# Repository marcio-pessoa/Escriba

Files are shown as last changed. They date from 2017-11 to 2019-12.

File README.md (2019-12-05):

# Escriba Mark I - Light CNC

## Introduction

Escriba Mark I is a Light CNC machine, capable to use tools like Pens, Laser other kind of stuff.

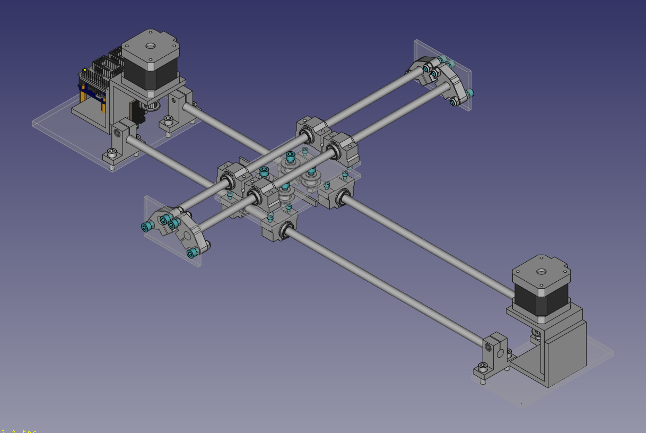
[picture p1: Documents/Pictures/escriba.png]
Escriba


<!---
The bidimentional work area:
- Width: ??? mm
- Height: ??? mm
--->

## Cloning
```
git clone --recurse-submodules https://github.com/marcio-pessoa/Escriba.git
```

## Videos
Watch this projects videos on [YouTube Playlist].

## Changes
All notable changes to this project will be documented in this [Change log](CHANGELOG.md).

## Mechanics
This project uses an original mech made from scratch with the following goals:
- Reliable
- Precise
- Robust
- Well done
- Cheap, but beautiful

Check out [Mechanics](Mechanics/README.md) design to know more.

## Electronics
Arduino and CNC Shield are used to [Electronics](Electronics/README.md) control system.

## Firmware
Grbl is my [Firmware](Firmware/README.md)! :-)

## Tools
Nice [Tools](Tools/README.md) can be used with!

## BOM - Bill of materials
If you want to build your own, take a look at [Bill of materials](BOM.md).

---
[YouTube Playlist]: https://www.youtube.com/watch?v=fAPBSzcztSE&list=PLs1JZHyVhlZUeYavBQfkzo5e3CdledMW0

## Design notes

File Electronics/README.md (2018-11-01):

# Escriba Mark I - Light CNC

[Main page]

## Electronics

### Power supply
Technical specifications:
- Voltage: 12 VDC
- Amperage: 5 A
- Interface: P8 (+ out, - in)

### Arduino
Technical specifications:
- Model: [Arduino Uno] R3

#### Diagram
                                 .-----.
    .----[PWR]-------------------| USB |--.
    |                            '-----'  |
    |         GND/RST2  [ ][ ]            |
    |       MOSI2/SCK2  [ ][ ]  A5/SCL[ ] |   C5
    |          5V/MISO2 [ ][ ]  A4/SDA[ ] |   C4
    |                             AREF[ ] |
    |                              GND[ ] |
    | [ ]NC                     SCK/13[ ] |   B5
    | [ ]v.ref                 MISO/12[ ] |   .
    | [ ]RST                   MOSI/11[ ]~|   .
    | [ ]3V3    +---+               10[ ]~|   .
    | [ ]5v     | A |                9[ ]~|   .
    | [ ]GND   -| R |-               8[ ] |   B0
    | [ ]GND   -| D |-                    |
    | [ ]Vin   -| U |-               7[ ] |   D7
    |          -| I |-               6[ ]~|   .
    | [ ]A0    -| N |-               5[ ]~|   .
    | [ ]A1    -| O |-               4[ ] |   .
    | [ ]A2     +---+           INT1/3[ ]~|   .
    | [ ]A3                     INT0/2[ ] |   .
    | [ ]A4/SDA  RST SCK MISO     TX>1[ ] |   .
    | [ ]A5/SCL  [ ] [ ] [ ]      RX<0[ ] |   D0
    |            [ ] [ ] [ ]              |
    '--.                         .--------'
        \_______________________/

Diagram by http://busyducks.com/ascii-art-arduinos

#### Pin designation
 id | pin |   type    | direction |               description
----|-----|-----------|-----------|--------------------------------------------
  0 |   0 | digital   | input     | Serial communication
  1 |   1 | digital   | output    | Serial communication
  2 |   0 | digital   | output    | Step Pulse x-axis
  3 |   3 | digital   | output    | Step Pulse y-axis
  4 |   4 | digital   | output    | Step Pulse z-axis
  5 |   5 | digital   | output    | Direction x-axis
  6 |   6 | digital   | output    | Direction y-axis
  7 |   7 | digital   | output    | Direction z-axis
  8 |   8 | digital   | output    | Stepper Enable/Disable
  9 |   9 | digital   | input     | Limit x-axis
 10 |  10 | digital   | input     | Limit y-axis
 11 |  11 | PWM       | input     | Limit z-axis
 12 |  12 | digital   | output    | Spindle Enable
 13 |  13 | digital   | output    | Spindle Direction
 14 |   0 | digital   | input     | Reset/Abort
 15 |   1 | digital   | input     | Feed Hold
 16 |   2 | digital   | input     | Cycle Start/Resume
 17 |   3 | digital   | output    | Coolant Enable
 18 |   4 | digital   | input     | (not used/reserved)
 19 |   5 | digital   | input     | Probe

### CNC Shield
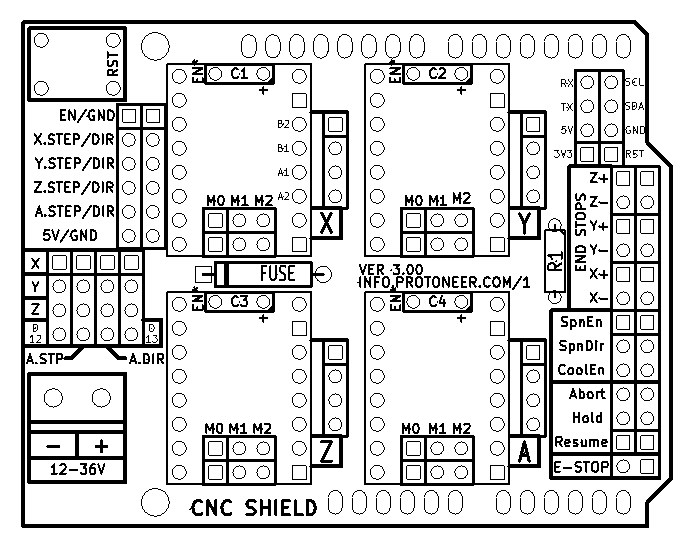
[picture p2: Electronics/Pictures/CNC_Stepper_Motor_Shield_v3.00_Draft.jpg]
PCB description


[CNC/Stepper Motor Shield](../Documents/cnc-3axis-shield.pdf)

Technical specifications:
- Version: 3.00

Connected at:
- Arduino: Digital Pin 11
- CNC Shield: Z+ end stop pin

### Stepper drivers
CNC Shield has 3 jumpers to configure each axes resolution.
That can be set to configure the motor micro stepping.

#### Resolution configuration

##### Pololu A4988
 M0   | M1   | M2   | Microstep resolution
------|------|------|-----------------------
 Low  | Low  | Low  | Full step
 High | Low  | Low  | Half step
 Low  | High | Low  | Quarter step
 High | High | Low  | Eighth step
 High | High | High | Sixteenth step

##### Pololu DRV8825
 M0   | M1   | M2   | Microstep resolution
------|------|------|-----------------------
 Low  | Low  | Low  | Full step
 High | Low  | Low  | Half step
 Low  | High | Low  | 1/4 step
 High | High | Low  | 1/8 step
 Low  | Low  | High | 1/16 step
 High | Low  | High | 1/32 step
 Low  | High | High | 1/32 step
 High | High | High | 1/32 step

### Step motors
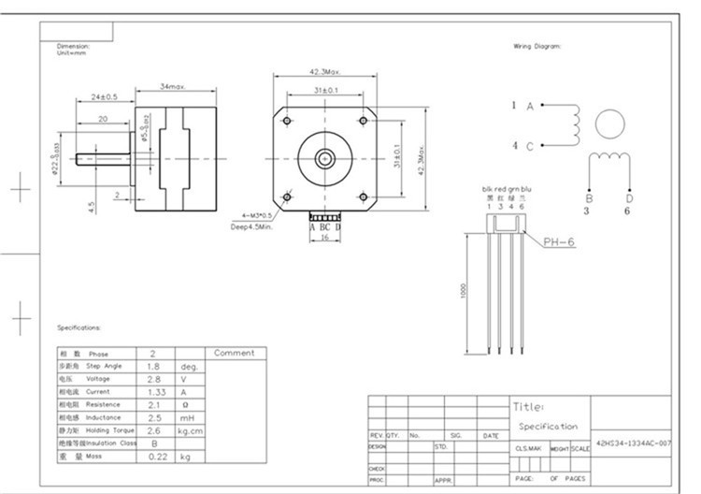
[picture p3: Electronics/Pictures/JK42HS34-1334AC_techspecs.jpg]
Step motors


Technical specifications:
- Model: JK42HS34-1334AC
- Phase: 2
- Step angle: 1.8 degrees (200 steps/revolution)
- Rated voltage: 2.8 V
- Current/Phase: 1.33 A
- Resistance/Phase: 2.1 Ω
- Inductance/Phase: 2.5 mH
- Holding Torque: 22 N·cm (2.6 kg·cm)
- Outlet: 4 wires
- Shaft: 5 mm single flat
- Size (metric): 4.2 cm x 4.2 cm x 3.4 cm
- Size (imperial): 1.65" x 1.65" x 1.34"

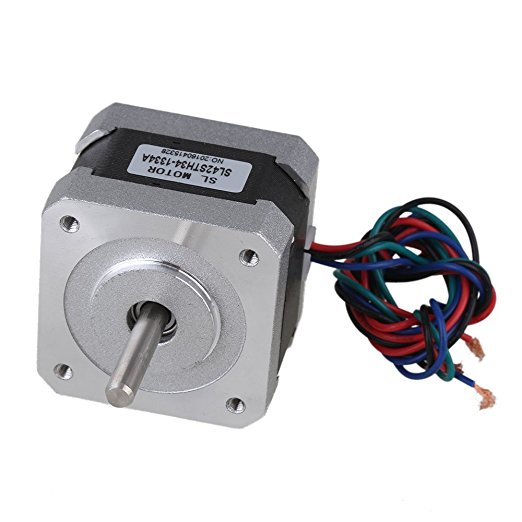
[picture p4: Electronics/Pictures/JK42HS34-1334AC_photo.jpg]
NEMA 17 step motor


### Fan driver
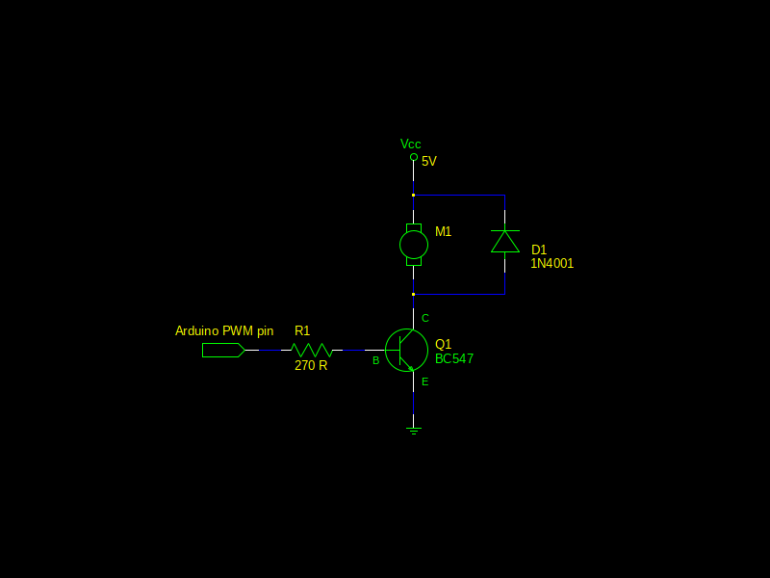
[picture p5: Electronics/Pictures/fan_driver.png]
Fan driver


[Fan driver schematic](fan_driver.sch) file (gEDA - GPL Electronic Design Automation).

[Main page]

---

[Arduino Uno]: https://www.arduino.cc/en/Main/arduinoBoardUno/#techspecs
[Main page]: ../README.md

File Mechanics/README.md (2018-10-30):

# Escriba Mark I - Light CNC

[Main page]

## Mechanics

### Technical specifications

Dimensions:
- Width:  mm
- Height:  mm
- Depth:  mm

Mass:
- Weight:  g (calculated)

Maximum travel:
- x axis: 394,20 mm (calculated)
- y axis: 213.15 mm (calculated)
- z axis: 0.0 mm (calculated)

Mechanical design

### Parts

#### SHF8
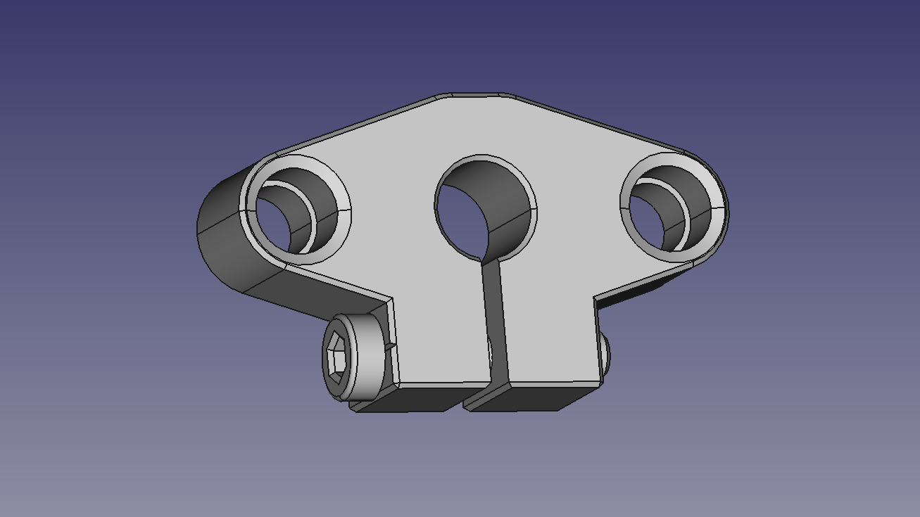
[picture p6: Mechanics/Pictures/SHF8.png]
SHF8


Technical specifications:
- Shaft: 8 mm
- Fastener: M5
- Material: aluminium

#### SC8VUU
Technical specifications:
- Shaft: 8 mm
- Fastener: M3
- Material: aluminium
- System: LM8UU

#### Belt
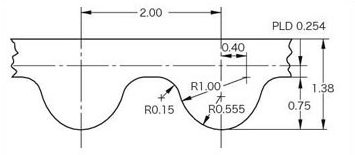
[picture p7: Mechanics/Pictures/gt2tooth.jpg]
GT2 belt


Technical specifications:
- Standard: GT2
- Pinch: 2 mm
- Wide: 6 mm
- Lenght:  mm

#### Noise reduction

[Main page]

---
[Main page]: ../README.md

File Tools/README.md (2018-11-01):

# Escriba Mark I - Light CNC

[Main page]

## Tools

### Pen
Pen holder
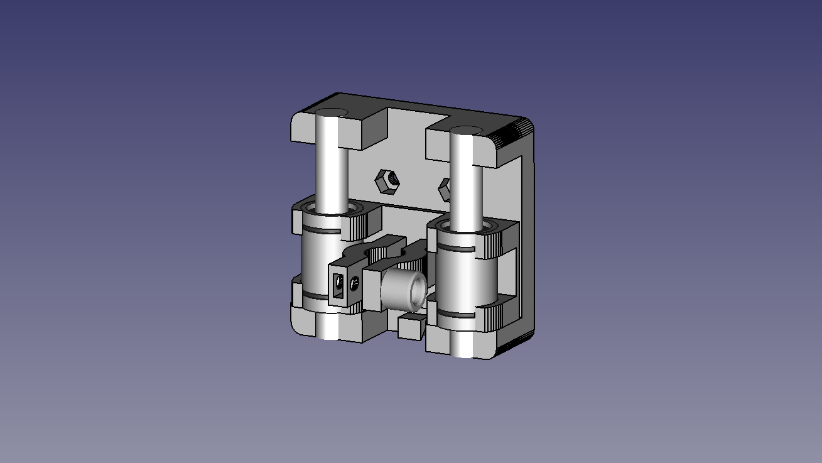
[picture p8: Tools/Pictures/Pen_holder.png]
Pen holder


<!---
Technical specifications:
- Material: ABS (3D printed) and steel
--->

### Laser
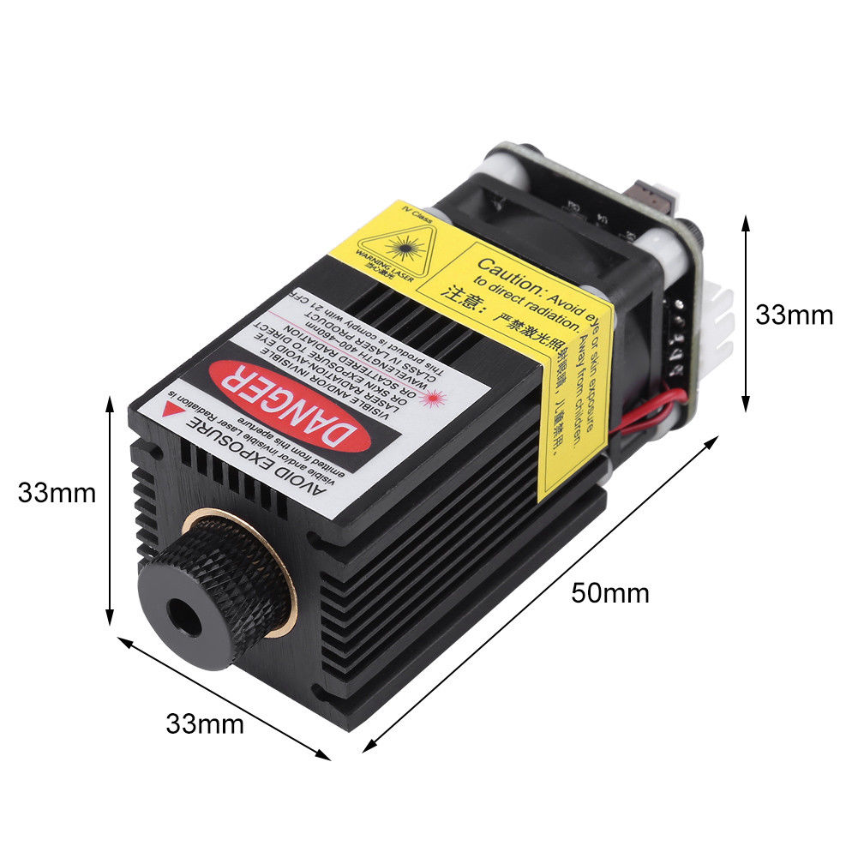
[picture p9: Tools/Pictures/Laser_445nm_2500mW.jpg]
Laser


Technical specifications:
- Power: 2.5 W
- Voltage: 12 VDC
- Version: 2
- PWM: Yes

<!---
#### Operation
 Material  | Power (mW) | Feed (ms)
-----------|------------|-----------
 Paper     |        980 |      1000
 Cardboard |            | 
 Foarm     |            | 
 Wood      |            | 
 Leather   |            | 
 Acrilic   |            | 
--->

[Main page]

---

[Main page]: ../README.md

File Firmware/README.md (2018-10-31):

# Escriba Mark I - Light CNC

[Main page]

# Firmware

## Grbl
> "Grbl is a no-compromise, high performance, low cost alternative to parallel-port-based motion control for CNC milling. It will run on a vanilla Arduino (Duemillanove/Uno) as long as it sports an Atmega 328.
>
> The controller is written in highly optimized C utilizing every clever feature of the AVR-chips to achieve precise timing and asynchronous operation. It is able to maintain up to 30kHz of stable, jitter free control pulses.
>
> It accepts standards-compliant g-code and has been tested with the output of several CAM tools with no problems. Arcs, circles and helical motion are fully supported, as well as, all other primary g-code commands. Macro functions, variables, and most canned cycles are not supported, but we think GUIs can do a much better job at translating them into straight g-code anyhow.
>
> Grbl includes full acceleration management with look ahead. That means the controller will look up to 18 motions into the future and plan its velocities ahead to deliver smooth acceleration and jerk-free cornering."
>
> -- From: [Grbl web page]

### Configuring
Use a terminal software and set the baud rate to 115200 as 8-N-1 (8-bits, no parity, and 1-stop bit.)

Recomended values are in [default.gcode](../Configuration/default.gcode).

[Grbl configuring]

### G-Code
List of Supported G-Codes:
  <!--- - Non-Modal Commands: G4, G10L2, G10L20, G28, G30, G28.1, G30.1, G53, G92, G92.1--->
  - Motion Modes: G0, G1, G2, G3, G38.2, G38.3, G38.4, G38.5, G80
  <!--- - Feed Rate Modes: G93, G94--->
  - Unit Modes: G20, G21
  - Distance Modes: G90, G91
  <!--- - Arc IJK Distance Modes: G91.1--->
  <!--- - Plane Select Modes: G17, G18, G19--->
  <!--- - Tool Length Offset Modes: G43.1, G49--->
  <!--- - Cutter Compensation Modes: G40--->
  <!--- - Coordinate System Modes: G54, G55, G56, G57, G58, G59--->
  - Control Modes: G61
  - Program Flow: M0, M1, M2, M30*
  - Coolant Control: M8, M9
  <!--- - Spindle Control: M3, M4, M5--->
  - Valid Non-Command Words: F, I, J, K, L, N, P, R, S, T, X, Y, Z

### Control

#### Spindle
Spindle are controled using PWM PIN 11 to drive the tool.

Use the command Sxxx (xxx between 0 and 2500) to:
  - Set laser (2500 mW) intensity.
  - Rotate servo between 0 and 180 degrees.

##### M3
- Constant laser power mode simply keeps the laser power as programmed, regardless if the machine is moving, accelerating, or stopped. This provides better control of the laser state. With a good G-code program, this can lead to more consistent cuts in more difficult materials.

- For a clean cut and prevent scorching with M3 constant power mode, it's a good idea to add lead-in and lead-out motions around the line you want to cut to give some space for the machine to accelerate and decelerate.

NOTE: M3 can be used to keep the laser on for focusing.

##### M4
- Dynamic laser power mode will automatically adjust laser power based on the current speed relative to the programmed rate. It essentially ensures the amount of laser energy along a cut is consistent even though the machine may be stopped or actively accelerating. This is very useful for clean, precise engraving and cutting on simple materials across a large range of G-code generation methods by CAM programs. It will generally run faster and may be all you need to use.

- Grbl calculates laser power based on the assumption that laser power is linear with speed and the material. Often, this is not the case. Lasers can cut differently at varying power levels and some materials may not cut well at a particular speed and/power. In short, this means that dynamic power mode may not work for all situations. Always do a test piece prior to using this with a new material or machine.

- When not in motion, M4 dynamic mode turns off the laser. It only turns on when the machine moves. This generally makes the laser safer to operate, because, unlike M3, it will never burn a hole through your table, if you stop and forget to turn M3 off in time.

##### M5
The command M05 set PWM to PIN 11 to zero.

##### Aditional information
You can change the pulse duration in the file spindle_control.c:

``` c++
define RC_SERVO_SHORT 15 // Timer ticks for 0.6ms pulse duration (9 for 0.6ms)
define RC_SERVO_LONG 32 // Timer ticks for 2.5 ms pulse duration (39 for 2.5ms)
define RC_SERVO_INVERT 1 // Uncomment to invert servo direction
```
If you want to have the servo working from 0 --> 180 degrees change RC_SERVO_SHORT and put 9, RC_SERVO_LONG and put 39 If you want invert the servo direction uncomment the line above.

https://github.com/gnea/grbl/wiki/Grbl-v1.1-Laser-Mode

https://github.com/gnea/grbl/wiki/Grbl-v1.1-Jogging

https://github.com/gnea/grbl/wiki/Grbl-v1.1-Configuration

#### Fan

##### M8

##### M9

[Main page]

---

[Grbl web page]: https://github.com/gnea/grbl
[Grbl configuring]: https://github.com/gnea/grbl/wiki/Grbl-v1.1-Configuration
[Main page]: ../README.md

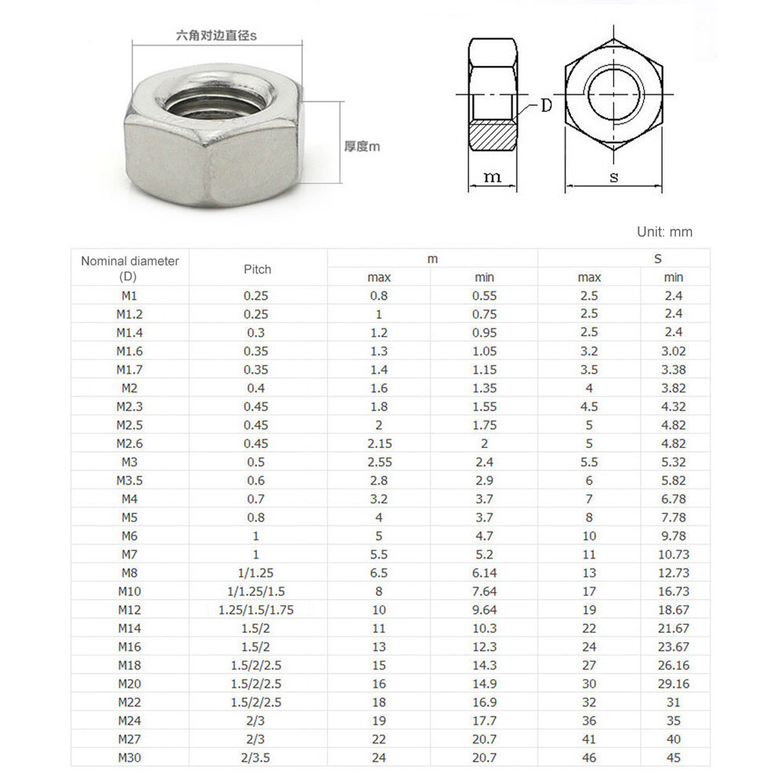
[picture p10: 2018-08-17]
Mechanics/Pictures/s-l1600s.jpg

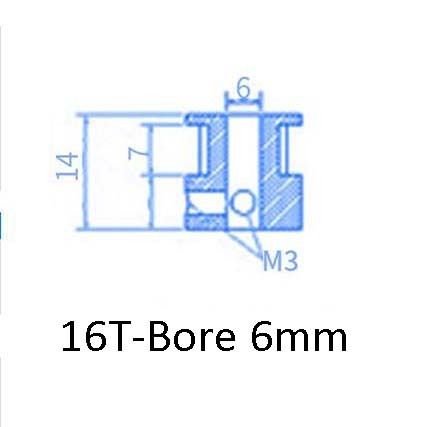
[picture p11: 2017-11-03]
Mechanics/Pictures/s-l1600.jpg

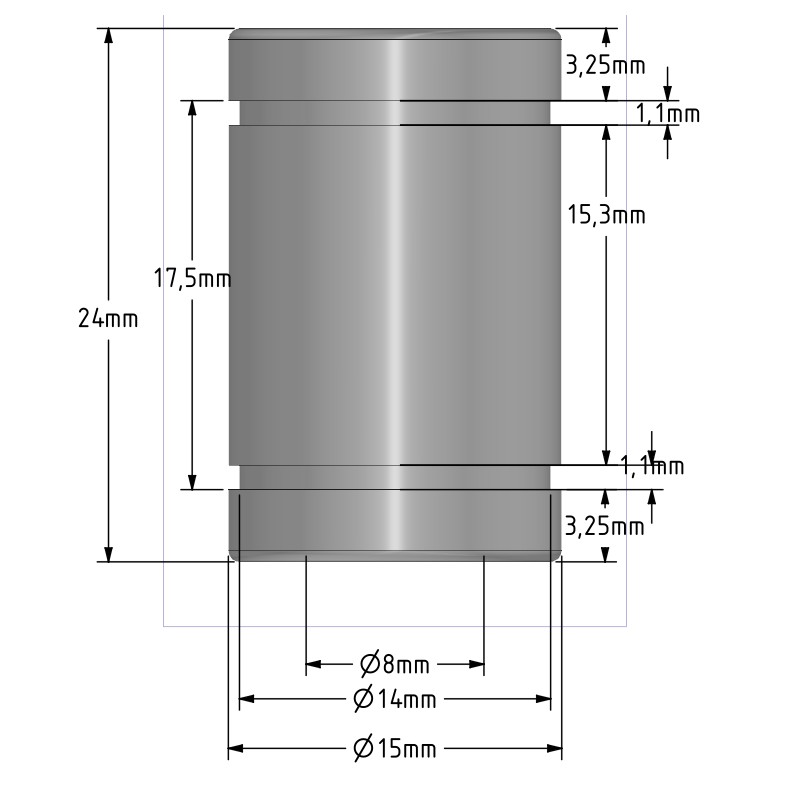
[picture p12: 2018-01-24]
Mechanics/Pictures/linear-bearing-lm8uu-for-8mm-smooth-shafts.jpg

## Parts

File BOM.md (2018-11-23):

# BOM
Escriba Mark I - Light CNC, Bill of materials

## Purchased
| Quant | Description | ID | Bought | Delivered  | Unit | Charge | Taxes | Cost |
|---|---|---|---|---|---|---|---|---|
| 1 | Arduino_Uno_R3 |  1461804416006 | 2016-10-09 | 2016-11-29 | each | 7.82 |  0.49 | 8.31 |
| 1 | CNC_Shield | 112401201692 | 2017-08-17 | 2018-01-23 | each | 7.40 |  0.46 | 7.86 |
| 500 | Chromed_rod_8mm | 322133935331 | 2016-08-02 | 2016-10-10 | mm | 5.78 |  0.38 | 6.15 |
| 400 | Chromed_rod_8mm | 322133935331 | 2016-10-19 | 2016-11-17 | mm |  11.58 |  0.73 |  12.31 |
| 400 | Chromed_rod_8mm | 322133935331 | 2016-10-19 | 2016-11-17 | mm | 0.00 |  0.00 | 0.00 |
| 200 | GT2_Belt_6mm | 272234427429 | 2016-09-09 | 2016-10-25 | cm | 7.68 |  0.48 | 8.16 |
| 2 | GT2_16T | 272234427429 | 2016-09-09 | 2016-10-25 | each | 0.00 |  0.00 | 0.00 |
| 4 | GT2_20N_pulley | 131648026845 | 2016-07-21 | 2016-09-dd | each |  10.98 |  0.69 |  11.67 |
| 1 | GT2_20T_pulley | 282052333232 | 2016-08-09 | 2016-09-1d | each | 2.35 |  0.14 | 2.49 |
| 1 | NEMA17_stepper | 331871059726 | 2019-09-25 | 2016-10-28 | each |  10.38 |  0.66 |  11.04 |
| 1 | NEMA17_stepper | 331871062088 | 2016-10-29 | 2017-mm-dd | each |  10.38 |  0.66 |  11.04 |
| 2 | NEMA17_fastener | 322123572546 | 2016-09-25 | 2016-11-17 | each | 7.87 |  0.50 | 8.37 |
| 2 | NEMA17_fastener | 162212160256 | 2017-04-13 | 2016-11-17 | each |  12.50 |  0.79 |  13.29 |
| 1 | GT2_Belt_holder | 112057548112 | 2016-10-09 | 2017-01-12 | each | 2.71 |  0.17 | 2.88 |
| 8 | SC8VUU | 110723291022 | 2016-08-09 | 2016-09-20 | each |  18.04 |  1.15 |  19.19 |
| 4 | SHF8 |  1442826626010 | 2016-10-30 | 2017-01-03 | each | 7.78 |  0.49 | 8.27 |
| 4 | SK8 |  1611059252007 | 2016-10-29 | 2017-01-05 | each | 4.74 |  0.30 | 5.04 |
| 2 | SK8 | 121970347137 | 2017-05-16 | 2017-mm-dd | each | 2.85 |  0.18 | 3.03 |
| 4 | Optical_endstop | 381842310412 | 2016-12-22 | 2017-05-18 | each | 3.21 |  0.20 | 3.41 |
| 1 | Acrylic_Sheet | 311663453699 | 2017-01-09 | 2017-03-27 | each | 5.89 |  0.37 | 6.26 |
| 1 | Acrylic_Sheet | 311663453699 | 2017-01-11 | 2017-07-12 | each | 5.89 |  0.37 | 6.26 |
| 1 | Acrylic_Sheet | 311663453699 | 2017-01-11 | 2017-07-12 | each | 5.89 |  0.37 | 6.26 |
| 1 | Acrylic_Sheet | 132109680453 | 2017-04-25 | 2017-05-18 | each | 5.89 |  0.37 | 6.26 |
| 1 | Laser_445nm_2500mW | 172860668862 | 2017-10-14 | 2017-11-27 | each |  78.22 |  4.99 |  83.21 |
| 1 | Felt_tip_pen | - | 2017-08-dd | 2017-08-dd | each | 0.00 |  1.00 | 1.00 |
|     1 | Fountain_pen   | -              | 2018-02-08 | 2018-02-08 | each |   6.08 |  0.00 |   6.08 |
| 8 | Adhesive_Feet | - | 2014-dd-dd | 2014-dd-dd | each | 0.00 |  0.00 | 0.00 |
| 1 | PSU_12VDC/5A | - | 2015-mm-dd | 2015-mm-dd | each | 0.00 |  0.00 | 0.00 |
| 1 | Laser_Glasses | 87215394438514 | 2017-10-14 | 2018-03-08 | each |  19.84 |  0,07 |  19.91 |
| 4 | Washer_M4 | 172371032208 | 2017-08-15 | 2018-03-26 | each | 0.09 |  0.01 | 0.10 |
| 50 | M3_spring_lock | 171955312322 | 2016-10-30 | 2017-03-21 | each | 1.44 |  0.09 | 1.53 |
| 16 | Nut_M3_nylon | 222111255325 | 2017-04-25 | 2017-07-dd | each | 1.72 |  0.10 | 1.82 |
| 14 | Nut_M5_nylon | 222111255325 | 2017-04-25 | 2017-07-dd | each | 1.40 |  0.08 | 1.48 |
| 30 | Screw_M3x10mm | 331767263691 | 2016-02-05 | 2016-xx-xx | each | 0.99 |  0.06 | 1.05 |
| 30 | Screw_M3x10mm | 331767263691 | 2016-02-05 | 2016-xx-xx | each | 0.99 |  0.06 | 1.05 |
| 16 | Screw_M3x14mm | 172087332352 | 2017-04-25 | 2017-05-dd | each | 1.82 |  0.11 | 1.93 |
| 16 | Screw_M4x10mm | 182015074419 | 2017-04-25 | 2017-05-dd | each | 2.04 |  0.13 | 2.17 |
| 24 | Screw_M4x14mm | 182015074419 | 2017-08-15 | 2018-03-26 | each | 3.79 |  0.24 | 4.03 |
| 16 | Screw_M5x14mm | 182093863816 | 2017-04-25 | 2017-05-dd | each | 2.18 |  0.13 | 2.31 |
| 10 | Screw_M5x14mm | 182093863816 | 2017-05-16 | 2017-07-dd | each | 2.17 |  0.13 | 2.30 |
| 10 | Screw_M5x16mm | 182093863816 | 2017-08-15 | 2018-03-26 | each | 2.36 |  0.15 | 2.51 |
| 20 | Screw_M5x20mm | 182093863816 | 2017-08-15 | 2018-03-26 | each | 2.62 |  0.09 | 0.09 |
| 10 | Screw_M5x16mm | 222714655541 | 2017-12-23 | 2018-04-28 | each | 1.77 |  0.11 | 1.88 |
| 10 | Screw_M5x20mm | 222714655541 | 2017-12-23 | 2018-04-28 | each | 2.05 |  0.13 | 2.18 |
| 10 | Screw_M5x25mm | 222714655541 | 2017-12-23 | 2018-04-28 | each | 2.05 |  0.13 | 2.18 |
| 10 | Screw_M4x25mm | 222714655541 | 2018-03-26 | 2018-06-04 | each | 1.79 |  0.10 | 1.89 |
| 8 | Screw_M5x18mm | 222714655541 | 2018-04-12 | 2018-07-dd | each | 2.30 |  0.15 | 2.45 |
| 1 | Screw_M6x16mm | 282782239986 | 2018-06-23 | 2018-07-31 | each | 1.03 | | |
| 1 | Quick_release_clamp  | 253256851967 | 2018-04-09 | 2018-06-06 | each | 7.04 |  0.45 | 7.49 |
| 1 | Quick_release_plate  | 253256851967 | 2018-04-09 | 2018-06-06 | each | 0.00 |  0.00 | 0.00 |
| 1 | Quick_release_plate  | 272048307553 | 2018-04-09 | 2018-06-20 | each | 2.91 |  0.11 | 3.02 |
| 2 | LM8UU | 370982181382 | 2017-12-09 | 2018-04-11 | each | 1.08 |  0.07 | 1.15 |
| 500 | Steel_tube_8x6mm | 390972746654 | 2018-04-12 | 2018-05-28 | mm | 8.33 |  0.49 | 8.82 |
| 1 | Servo_9g | 142920875158 | 2018-09-05 | 2018-10-23 | each | 2.08 |  0.12 | 2.20 |
| 1 | Pen_holder_parts | Pending | Pending | Pending | each | 0.00 |  0.00 | 0.00 |
| 10 | Elastic | Pending | Pending | Pending | each | 0.00 |  0.00 | 0.00 |

Currency: USD<br/>
International IOF: 6.38%<br/>
Domestic IOF: 0.38%

Total cost: $327.30

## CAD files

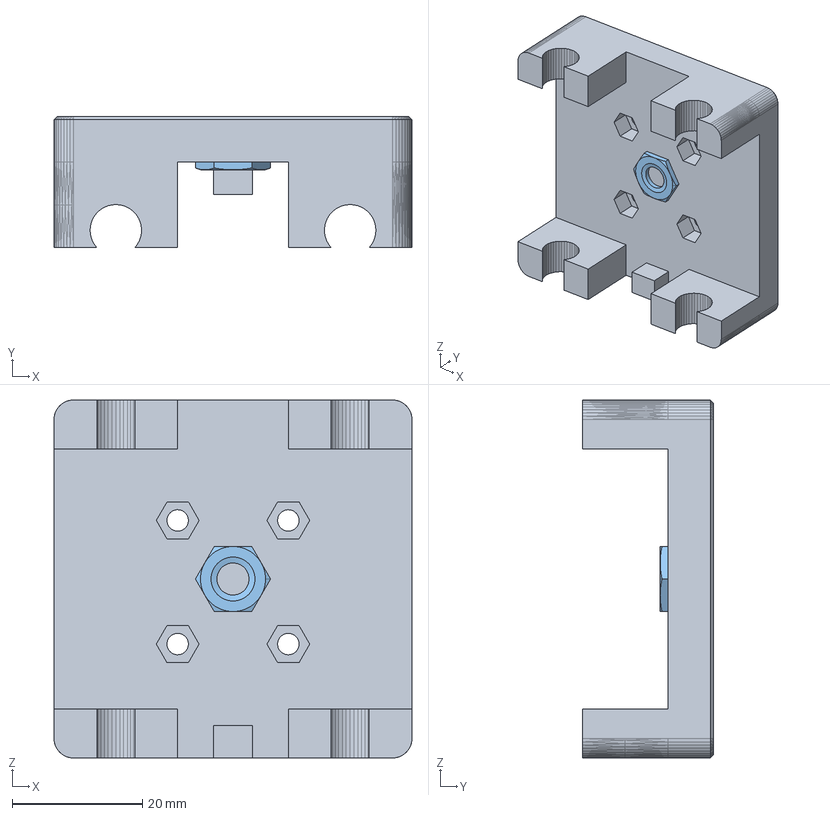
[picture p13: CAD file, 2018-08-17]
Mechanics/Pen_Holder.FCStd
55.0 x 20.2 x 55.0 mm
Pen_Holder_Base002
M6-Nut
M6-Nut001

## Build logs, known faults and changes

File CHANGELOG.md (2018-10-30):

# CHANGELOG
Escriba Mark I - Light CNC, Change log

## [1.1g] - 2018-09-05
### Added
- Fan.

### Changed
- Uploaded: Grbl 1.1g.

## [1.1f] - 2018-03-13
### Changed
- Uploaded: Grbl 1.1f.

## [0.9j] - 2017-09-12
### Added
- Enable: CoreXY.

### Changed
- Set: HOMING_CYCLE_0 to support COREXY.
- Set: SPINDLE_MAX_RPM to low rotation (tool speed).
- Disabled: HOMING_CYCLE_1 to support COREXY.

## [] - 2016-08-09
### Added
- Project definition.

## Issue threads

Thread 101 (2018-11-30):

Electronics - DRV8825 - Swap stepper motors drivers to better resolution

marcio-pessoa, 2018-11-30:

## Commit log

2017-11-03 Arduino code
2017-11-23 3D model
    [Escriba.fcstd]
2017-11-28 BOM file is not necessary any more
2017-12-24 Just renaming file extension
    [Escriba.fcstd]
2018-01-24 Add 'BOM.md'
2018-01-24 Starting a new BOM format
2018-01-24 Update 'BOM.md'
2018-01-24 Improved BOM
2018-01-24 Arduino schematic
2018-01-24 Updated BOM
2018-02-04 Minor updates.
    [Laser_Mount.stl, x3.sch]
2018-02-13 Minor updates
    [Laser_Mount.stl]
2019-12-05 Added GRBL as submodule
